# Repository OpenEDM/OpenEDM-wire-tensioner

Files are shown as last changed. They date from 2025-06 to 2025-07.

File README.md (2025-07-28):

# OpenEDM-wire-tensioner

This repository contains the design of the **Wire Tensioning Mechanism**, in particular, hardware design and firmware. Note that this design is a work in progress, it is not complete, and may contain errors.

Currently, the electronic hardware is assembled from heavily customized standard modules, as shown in the image below. An integrated hardware design is available in the [Hardware](https://github.com/OpenEDM/OpenEDM-wire-tensioner/tree/main/Hardware) directory, but it is still in the early stages of development.

The mechanical design of the wire tensioner is available as a part of the [OpenEDM-wire-machine design](https://github.com/OpenEDM/OpenEDM-wire-machine).



## Main design requirements

The wire tensioning mechanism must fulfill two main tasks:

1. Ensure that the wire in the cutting zone is fed according to the speed setpoint set by the user.
2. Ensure that the wire in the cutting zone is tensioned according to the tension setpoint set by the user.

## Operation principle

First, this is how the wire runs. On the right side (not shown in the photo) is the wire source; for example, a spool with new wire. On the left side (also not shown in the photo) is the location where the used wire is directed. This could be a spool for collecting the used wire, or a mechanism that cuts the wire into small pieces for convenient disposal:



Next, let's take a look at the wire tensioner's main components:



The wire enters the system through the **input wire feeder** (1). Then it passes around several passive pulleys. Next, the wire goes through the **wire guides** (6, 5). The **wire contacts** (7, 4), located near the wire guides, supply electricity to the wire. After that, the wire wraps around the last passive pulley, which is a part of the **load cell assembly** (10). Finally, the wire exits the system through the **output wire feeder** (8). All components are mounted on a frame, which consists of an **aluminum part** (2) and a **plastic part** (3). The system is controlled by an **electronic control unit** (9).

The system operates in such a way that the output feeder pulls the wire, while the input feeder, when necessary, slows the wire's movement by acting as a brake. The operation of the motors depends on the setpoints for speed and tension, as well as on the feedback signal from the load cell. More details are provided below.

There is an important design constraint for the input feeder: it must not deform the wire in any way, meaning it must not alter the shape of wire's cross-section. This constraint does not apply to the output feeder.

### Input wire feeder



To understand how this feeder works, let's look at how the wire is loaded into it. The wire enters the feeder through a PTFE tube connected to the **input fitting** (1.2). About one meter of wire should be pulled out from the tube, then placed into the groove of the **input latch** (1.1), and the latch should be closed. Next, the wire should be wrapped 4–5 times clockwise around the **pulley** (1.3). It doesn't matter if the loops are placed randomly; during operation, the feeder will self-correct their position. After that, without releasing the tension on the wire, the wire should be placed into the groove of the **output latch** (1.4) and the latch should be closed.

Some important points:
1. This feeder operates based on the [capstan effect](https://en.wikipedia.org/wiki/Capstan_equation).
1. For the feeder to operate correctly, the motor must rotate only clockwise, and there must always be some tension in the wire after the output latch.
1. Regarding the latches: the input and output latches are structurally identical. The input latch is shown in the closed position in the picture above, while the output latch is shown open. A closed latch significantly hinders the wire from passing through but does not block its movement completely.

### Output wire feeder



In this feeder, the main components are the pulleys, between which the wire is clamped. **Active puley** (8.6) is mounted directly on the motor shaft. **Passive puley** (8.7) is mounted on the **lever** (8.1) which rotates around the **axis** (8.3). Both pulleys have toothed rims that provide a kinematic connection between them. A **spring** (8.4), which presses against the **stop** (8.5), applies force to the lever, pushing the pulleys together and ensuring that the wire clamped between them cannot slip.

Again, let’s look at how the wire is loaded into this feeder. First, the lever (8.1) must be pressed to create a gap between pulleys (8.6) and (8.7). Then, the wire should be inserted into the hole marked with a red arrow. After that, the wire should pass between the pulleys and exit through the **output fitting** (8.2). Finally, the lever should be released so that the wire is clamped between the pulleys.

The main feature of this design is the construction of the pulleys. The pulleys must meet the following key requirements:

1. The surface that comes into contact with the wire must be hard enough so that the wire does not leave marks or cause deformation.
1. The pulleys must have an integrated toothed rim.

If the pulleys were made entirely of metal, manufacturing them would be a complex and costly task. However, a workaround was found that significantly simplifies the situation and reduces the cost. Each pulley is an assembly of three components:

1. An **outer bushing** (8.6.3) and an **inner bushing** (8.6.1). These bushings must be made of steel. However, due to their simple geometry, they can easily be sourced as off-the-shelf parts.
1. An **intermediate bushing** (8.6.2) with an integrated toothed rim. This bushing can simply be 3D-printed from a sufficiently strong plastic, such as ABS.

All three bushings -- outer, inner, and intermediate -- are press-fitted into one another. Of course, the dimensions of the plastic bushing must be chosen carefully to ensure a tight fit. This solution has been tested and has proven to work reliably in practice.

Another interesting aspect is the placement of the spring. It is easy to notice that the design of this feeder resembles that of a standard 3D printer extruder, for example, like [this one](https://youtu.be/zdTyMRBLIl4?t=35). However, in a typical 3D printer extruder, the spring is usually located inside, between the levers. In this design, the spring is placed on the outside.

The reason for this is that, for the feeder to work reliably, the pulleys axes must remain parallel, even when the spring applies significant pressure to the moving lever. Experiments have shown that the design with an externally mounted spring performs better in this regard.

### Load cell assembly



There is nothing particularly special about this part of the design. The **load cell** (10.2) is mounted on the wire tensioner frame using a **plastic holder** (10.1). The **passive pulley** (10.3) is attached to the load cell via another **plastic holder** (10.4).

The only noteworthy detail here is that the cable connecting the load cell to the electronic control unit is shielded, and the shield is electrically connected to the load cell beam. Often, the load cell beam is made of anodized aluminum, which prevents proper electrical contact; therefore, the anodized layer must be locally removed before connecting the cable shield to the beam.

### Control system operation algorithm

The current firmware version is located in the [corresponding folder](https://github.com/OpenEDM/OpenEDM-wire-tensioner/tree/main/Firmware). Below is a brief description of how it works:

Immediately after power is applied, the device performs a tare operation on the load cell. At this point, it is assumed that the wire is already loaded into the system. The input motor does not rotate. The output motor rotates in reverse to reduce the wire tension in the system. This reverse motion continues until the reading from the load cell stops changing. After that, the load cell is tared, and the device enters normal operation mode.

During normal operation, the following occurs:

1. The speed of the input motor depends only on the wire feed rate setpoint.
1. The speed of the output motor is controlled by a PID regulator, which receives the tension error as input -- that is, the difference between the actual tension (measured by the load cell) and the target tension set by the user.
1. The motors operate only if the output of the load cell exceeds a threshold value (by default, 500 grams). If the load cell reads below this threshold, it most likely indicates a broken wire, and the motors remain stopped.

## Electronic control unit

The electronic control unit is currently assembled from the following components:

1. NUCLEO-L432KC STM32 devboard.
1. (2x) TMC2209 stepper motor driver. The microstepping should be set to 1/16. The current should be set according to the motors.
1. SparkFun HX711 load cell amplifier. Should be modified according to the info below.

Here is the SparkFun HX711 schematic:



The following changes should be introdiced:

1. C1 should be replaced with 6.8u. The will change the LPF (C1, R3, R4) cutoff frequency to ~117Hz.
1. SJ2 should be opened so the data rate is 80SPS.

In addition to that, the shield of the load cell cable should be connected to JP4.1. These measures -- modifying the board and connecting the cable shield -- are necessary to reduce the influence of electromagnetic noise generated by the EDM on the load cell readings.

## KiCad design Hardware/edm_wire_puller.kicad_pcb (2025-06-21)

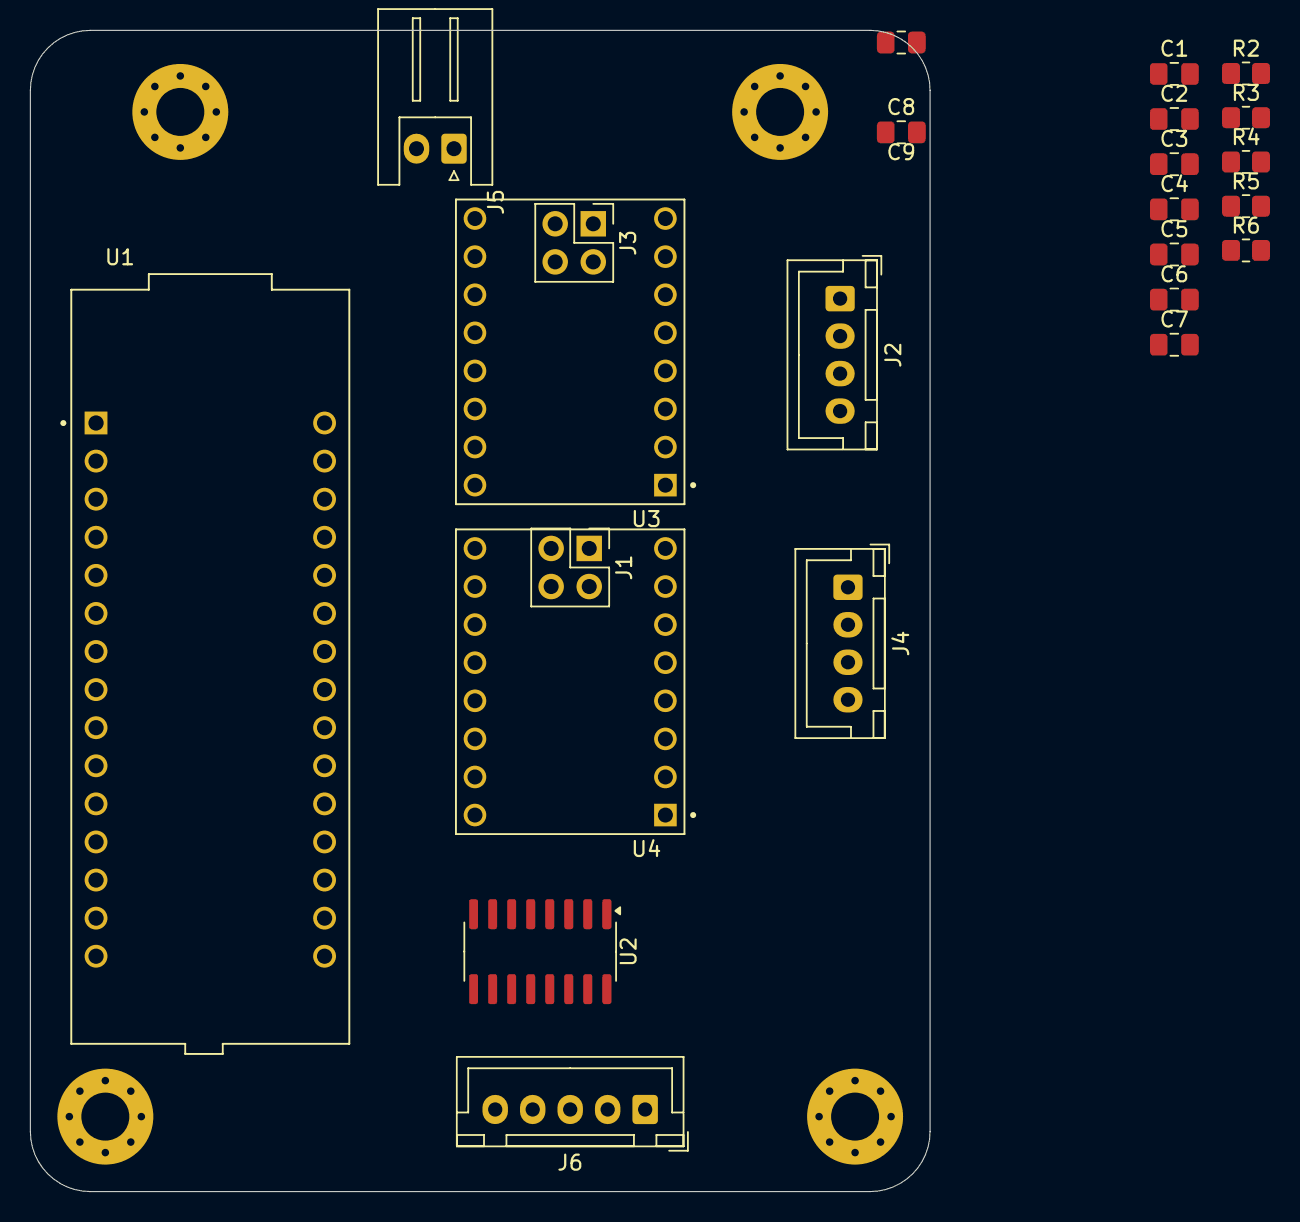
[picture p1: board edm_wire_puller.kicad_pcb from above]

Board: 2 copper layers, 60.0 x 77.4 mm, 28 parts (0 on the bottom side), 24 nets, no tracks yet.

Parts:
C1, C2, C4, C6: 0.1u; C_0805_2012Metric_Pad1.18x1.45mm_HandSolder
C3: 6.8u; C_0805_2012Metric_Pad1.18x1.45mm_HandSolder
C5, C7: 10u; C_0805_2012Metric_Pad1.18x1.45mm_HandSolder
C8, C9: 1u; C_0805_2012Metric_Pad1.18x1.45mm_HandSolder
H1, H2, H3, H4: MountingHole_Pad; MountingHole_3.2mm_M3_Pad_Via
J1, J3: Conn_02x02_Top_Bottom; PinHeader_2x02_P2.54mm_Vertical
J2, J4: Conn_01x04; JST_XH_B4B-XH-A_1x04_P2.50mm_Vertical
J5: Conn_01x02; JST_XH_S2B-XH-A_1x02_P2.50mm_Horizontal
J6: Conn_01x05; JST_XH_B5B-XH-A_1x05_P2.50mm_Vertical
R2: 20k; R_0805_2012Metric_Pad1.20x1.40mm_HandSolder
R3: 8.2k; R_0805_2012Metric_Pad1.20x1.40mm_HandSolder
R4, R5: 100; R_0805_2012Metric_Pad1.20x1.40mm_HandSolder
R6: 10k; R_0805_2012Metric_Pad1.20x1.40mm_HandSolder
U1: NUCLEO-L412KB; MODULE_NUCLEO-L412KB
U2: HX711; SOP-16_3.9x9.9mm_P1.27mm
U3, U4: TMC2209; MODULE_TMC2209

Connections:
+5V: C1.1, C6.1, C7.1, J1.1, J1.2, J3.1, J3.2, R6.2, U2.1 (VSUP), U2.16 (DVDD), U3.2 (VIO), U4.2 (VIO)
+12V: J5.1, U3.8 (VM), U4.8 (VM)
A+: J6.4, R5.1
A-: J6.3, R4.2
E+: C4.2, C5.2, J6.1
GND: C1.2, C2.2, C4.1, C5.1, C6.2, C7.2, C8.2, C9.2, J5.2, J6.2, J6.5, R3.2, U1.CN4_2 (GND), U2.5 (AGND), U2.9 (INB-), U2.10 (INB+), U2.14 (XI), U3.1 (GND), U3.7 (GND), U4.1 (GND), U4.7 (GND)
M1_1A: J2.3, U3.4 (M1A)
M1_1B: J2.4, U3.3 (M1B)
M1_2A: J2.2, U3.5 (M2A)
M1_2B: J2.1, U3.6 (M2B)
M2_1A: J4.3, U4.4 (M1A)
M2_1B: J4.4, U4.3 (M1B)
M2_2A: J4.2, U4.5 (M2A)
M2_2B: J4.1, U4.6 (M2B)
unnamed: J1.3, U4.15 (MS1)
unnamed: J1.4, U4.14 (MS2)
unnamed: J3.3, U3.15 (MS1)
unnamed: J3.4, U3.14 (MS2)
unnamed: R6.1, U2.15 (RATE)
unnamed: R2.2, U2.3 (AVDD)
unnamed: C3.1, C8.1, C9.1, R5.2, U2.8 (INA+)
unnamed: C3.2, R4.1, U2.7 (INA-)
unnamed: C2.1, U2.6 (VBG)
unnamed: R2.1, R3.1, U2.4 (VFB)

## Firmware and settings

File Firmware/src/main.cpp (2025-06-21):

#include <Arduino.h>
#include <Debounce.h>
#include <HX711.h>
#include <QuickPID.h>
#include "StepperMotor.h"

/***************************************/
/*************** BUTTONS ***************/
/***************************************/

constexpr size_t NUMBER_OF_BUTTONS  = 4;

constexpr int BUTTON_0              = 0;
constexpr int BUTTON_1              = 1;
constexpr int BUTTON_2              = 2;
constexpr int BUTTON_3              = 3;

constexpr int DEBOUNCE_DELAY_MS     = 30;

// Debounce buttons[] = {
//     Debounce(9, DEBOUNCE_DELAY_MS, true),
//     Debounce(10, DEBOUNCE_DELAY_MS, true),
//     Debounce(11, DEBOUNCE_DELAY_MS, true),
//     Debounce(12, DEBOUNCE_DELAY_MS, true),
// };

byte button_state[]                 = {0, 0, 0, 0};
byte button_state_previous[]        = {0, 0, 0, 0};

/***************************************/
/************** LOAD CELL **************/
/***************************************/

constexpr byte LOADCELL_DOUT_PIN        = D2;
constexpr byte LOADCELL_SCK_PIN         = D5;

HX711 loadcell;

constexpr long MIN_TENSION_G            = 500;
long actual_tension_g                   = 0;

constexpr long LOADCELL_SAMPLE_TIME_MS  = 10;

/***************************************/
/*************** MOTORS ****************/
/***************************************/

constexpr int PULLEY_RADIUS_MM      = 10;
constexpr int FULL_STEPS_PER_REV    = 200;
constexpr int MICROSTEPPING         = 16;

constexpr int STEPS_PER_REV         =  FULL_STEPS_PER_REV * MICROSTEPPING;
constexpr float STEPS_PER_MM        = FULL_STEPS_PER_REV * MICROSTEPPING / (2 * PI * PULLEY_RADIUS_MM);

constexpr direction_t DEFAULT_DIR   = COUNTER;

// constexpr int X_DIR_PIN             = D2;
constexpr int Y_DIR_PIN             = D3;
constexpr int Z_DIR_PIN             = D4;
// constexpr int X_STP_PIN             = D5;
constexpr int Y_STP_PIN             = D6;
constexpr int Z_STP_PIN             = A2; // D7

constexpr int SHIELD_EN_PIN         = D9; // D8

constexpr int MS1_PIN               = D12;
constexpr int MS2_PIN               = D11;

StepperMotor input_motor(Z_STP_PIN, Z_DIR_PIN);
StepperMotor output_motor(Y_STP_PIN, Y_DIR_PIN);

long output_motor_step_period_us;
long input_motor_step_period_us;

long output_motor_last_step_timestamp_us    = 0;
long input_motor_last_step_timestamp_us     = 0;

/***************************************/
/***************** PID *****************/
/***************************************/

constexpr int PID_LIMIT = 3000;

float pid_setpoint, pid_input, pid_output;

float pid_kp = 5.0f;
float pid_ki = 2.0f;
float pid_kd = 0.1f;

bool compute_ok         = false;

QuickPID PID(
    &pid_input, &pid_output, &pid_setpoint, 
    pid_kp, pid_ki, pid_kd, 
    QuickPID::pMode::pOnError, QuickPID::dMode::dOnError, 
    QuickPID::iAwMode::iAwClamp, 
    QuickPID::Action::reverse
);

/***************************************/
/*********** MAIN PARAMETERS ***********/
/***************************************/

int speed_setpoint_mmpersec = 2;
long tension_setpoint_g     = 2000;

/***************************************/
/***************************************/
/***************************************/

void calculate_motors_speed(int speed_setpoint_mmpersec) {
    int base_step_period_us = 1000000.0 / (STEPS_PER_MM * speed_setpoint_mmpersec);

    output_motor_step_period_us = base_step_period_us;
    input_motor_step_period_us = base_step_period_us;
}

/*
void process_buttons() {
    for (int i = 0; i < NUMBER_OF_BUTTONS; ++i) {
        button_state_previous[i] = button_state[i];
    }

    for (int i = 0; i < NUMBER_OF_BUTTONS; ++i) {
        button_state[i] = buttons[i].read();
    }

    if (button_state_previous[BUTTON_3] == LOW && button_state[BUTTON_3] == HIGH) {
        enable = !enable;
    }

    fast_wire_feeding = (button_state[BUTTON_0] == HIGH);
}
*/

// https://www.aliexpress.com/item/1005003288007057.html
void set_microstepping(int microstepping) {
    pinMode(MS1_PIN, OUTPUT);
    pinMode(MS2_PIN, OUTPUT);
    
    switch (microstepping)
    {
    case 8:
        digitalWrite(MS1_PIN, LOW);
        digitalWrite(MS2_PIN, LOW);
        break;
    case 16:
        digitalWrite(MS1_PIN, HIGH);
        digitalWrite(MS2_PIN, HIGH);
        break;
    case 32:
        digitalWrite(MS1_PIN, HIGH);
        digitalWrite(MS2_PIN, LOW);
        break;
    case 64:
        digitalWrite(MS1_PIN, LOW);
        digitalWrite(MS2_PIN, HIGH);
        break;
    
    default:
        for (;;){}
        break;
    }
}

long get_tension() {
    return loadcell.get_value() * 2750 / 618858;
}

void startup() {
    constexpr int step_delay_ms = 10;
    constexpr int backwards_steps = 30;
    constexpr int taring_times = 100;

    long tension = get_tension();
    long tension_prev = tension;

    // turn the output motor backwards until the tension is no longer changing
    output_motor.set_dir(DEFAULT_DIR == COUNTER ? CLOCKWISE : COUNTER);

    do {
        tension_prev = tension;
        output_motor.steps(backwards_steps, step_delay_ms);
        tension = get_tension();
    } while (abs(tension - tension_prev) > 0);

    // tare the loadcell
    loadcell.tare(taring_times);

    // turn the output motor forwards until the tension is more than MIN_TENSION_G
    output_motor.set_dir(DEFAULT_DIR);
    
    do {
        output_motor.step();
        delay(step_delay_ms);
        tension = get_tension();
    } while (tension < MIN_TENSION_G);
}

void setup() {
    // startup delay
    delay(2000);

    Serial.begin(115200);

    pinMode(LED_BUILTIN, OUTPUT);

    input_motor.init();
    output_motor.init();

    StepperMotor::init_enable(SHIELD_EN_PIN);
    StepperMotor::enable();

    set_microstepping(MICROSTEPPING);

    loadcell.begin(LOADCELL_DOUT_PIN, LOADCELL_SCK_PIN);
    // loadcell.tare();

    PID.SetSampleTimeUs(LOADCELL_SAMPLE_TIME_MS * 1000);
    PID.SetOutputLimits(-PID_LIMIT, PID_LIMIT);
    PID.SetMode(QuickPID::Control::timer);

    startup();
}

void loop() {
    // process_buttons();
    
    long now = micros();

    if (actual_tension_g > MIN_TENSION_G) {
        if (now - output_motor_last_step_timestamp_us > output_motor_step_period_us) {
            output_motor_last_step_timestamp_us = now;

            output_motor.set_dir(DEFAULT_DIR);
            output_motor.step();
        }

        if (now - input_motor_last_step_timestamp_us > input_motor_step_period_us) {
            input_motor_last_step_timestamp_us = now;

            input_motor.set_dir(DEFAULT_DIR);
            input_motor.step();
        }
    }

    if (loadcell.is_ready()) {
        actual_tension_g = get_tension();

        if (actual_tension_g > MIN_TENSION_G) {
            pid_setpoint = tension_setpoint_g;
            pid_input = actual_tension_g;

            PID.SetTunings(pid_kp, pid_ki, pid_kd);
            compute_ok = PID.Compute();

            calculate_motors_speed(speed_setpoint_mmpersec);

            output_motor_step_period_us += pid_output;
        }
    }
}

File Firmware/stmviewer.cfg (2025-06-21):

[elf]
file_path = C:/projects_git/EDM/stepper_motor_controller/.pio/build/stm32/firmware.elf

[settings]
version = 1
sample_frequency_hz = 1000
max_points = 10000
max_viewport_points = 10000
refresh_on_elf_change = true
stop_acq_on_elf_change = false
probe_type = 0
target_name = 
probe_mode = 0
probe_speed_khz = 10000
probe_sn = 0672FF383834434257092311

[trace_settings]
core_frequency = 160000
trace_prescaler = 10
max_points = 10000
max_viewport_points_percent = 10
trigger_channel = -1
trigger_level = 0.900000
timeout = 2

[var0]
name = actual_tension_g
address = 536871616
type = 6
color = 1882090084

[var1]
name = compute_ok
address = 536871560
type = 1
color = 2606029026

[var2]
name = enable
address = 536870988
type = 0
color = 984614383

[var3]
name = output_motor_step_period_us
address = 536871588
type = 6
color = 3616096982

[var4]
name = pid_kd
address = 536870988
type = 7
color = 2295216214

[var5]
name = pid_ki
address = 536870992
type = 7
color = 3839796486

[var6]
name = pid_kp
address = 536870996
type = 7
color = 3620647178

[var7]
name = speed_setpoint_mmpersec
address = 536870984
type = 6
color = 57878452

[var8]
name = tension_setpoint_g
address = 536870980
type = 6
color = 4142905287

[plot0]
name = new plot0
visibility = true
type = 0

[plot0-series0]
name = actual_tension_g
visibility = true
format = DEC

[plot1]
name = new plot1
visibility = true
type = 2

[plot1-series0]
name = actual_tension_g
visibility = true
format = DEC

[plot1-series1]
name = compute_ok
visibility = true
format = DEC

[plot1-series2]
name = enable
visibility = true
format = DEC

[plot1-series3]
name = pid_kd
visibility = true
format = DEC

[plot1-series4]
name = pid_ki
visibility = true
format = DEC

[plot1-series5]
name = pid_kp
visibility = true
format = DEC

[plot1-series6]
name = speed_setpoint_mmpersec
visibility = true
format = DEC

[plot1-series7]
name = tension_setpoint_g
visibility = true
format = DEC

[plot2]
name = new plot2
visibility = true
type = 0

[plot2-series0]
name = output_motor_step_period_us
visibility = true
format = DEC

[trace_plot0]
name = CH0
alias = CH0
visibility = true
domain = 1

[trace_plot1]
name = CH1
alias = CH1
visibility = true
domain = 1

[trace_plot2]
name = CH2
alias = CH2
visibility = true
domain = 1

[trace_plot3]
name = CH3
alias = CH3
visibility = true
domain = 1

[trace_plot4]
name = CH4
alias = CH4
visibility = true
domain = 1

[trace_plot5]
name = CH5
alias = CH5
visibility = true
domain = 1

[trace_plot6]
name = CH6
alias = CH6
visibility = true
domain = 1

[trace_plot7]
name = CH7
alias = CH7
visibility = true
domain = 1

[trace_plot8]
name = CH8
alias = CH8
visibility = true
domain = 1

[trace_plot9]
name = CH9
alias = CH9
visibility = true
domain = 1

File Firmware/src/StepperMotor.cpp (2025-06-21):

#include "StepperMotor.h"
#include "Arduino.h"

int StepperMotor::enable_pin = 0;

StepperMotor::StepperMotor(int stp_pin, int dir_pin)
{
    this->stp_pin = stp_pin;
    this->dir_pin = dir_pin;
}

void StepperMotor::init()
{
    pinMode(stp_pin, OUTPUT);
    pinMode(dir_pin, OUTPUT);
}

void StepperMotor::set_dir(direction_t dir)
{
    this->dir = dir;
    digitalWrite(dir_pin, dir);
}

void StepperMotor::step()
{
    digitalWrite(stp_pin, HIGH);
    digitalWrite(stp_pin, LOW);
}

void StepperMotor::steps(int number_of_steps, int delay_ms)
{
    for (int i = 0; i < number_of_steps; ++i) {
        step();
        delay(delay_ms);
    }
}

void StepperMotor::init_enable(int enable_pin)
{
    StepperMotor::enable_pin = enable_pin;
    pinMode(StepperMotor::enable_pin, OUTPUT);
}

void StepperMotor::enable()
{
    digitalWrite(StepperMotor::enable_pin, LOW);
}

void StepperMotor::disable()
{
    digitalWrite(StepperMotor::enable_pin, HIGH);
}
